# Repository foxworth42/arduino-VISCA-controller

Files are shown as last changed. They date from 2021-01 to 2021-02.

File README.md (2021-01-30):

# Arduino VISCA Controller

## The project is a work-in-progress

This is a project for using an Arduino to send VISCA commands.  This is tailored for interfacing with the
Cisco TelePresence PrecisionHD series of conference cameras (specifically testing with the TTC8-02 12x zoom w/ SDI output).

The TelePresence cameras have a slight quirk to controlling it over VISCA.  To get manual control over the pan/tilt/zoom
rates the camera needs to be sent the IR disable command, otherwise all movements behave with a speed ramp as if you 
were controlling it with an IR remote.

The Arduino Shield board present in the EAGLE directory is intended to make connecting to a TelePresence camera and
wiring I/O easier.  The shield has headers to allow for powering the Arduino off its internal voltage regulator or via
VIN (includes header points to make swapping easy).  There is also a header to provide 12v power over the RJ45
connection to remotely power the camera.  The shield incudes an RS232 transciever so it is ready to plug into the
camera's control port with a standard ethernet cable.

[Cisco TelePresence PrecisionHD User Guide](https://www.cisco.com/c/dam/en/us/td/docs/telepresence/endpoint/camera/precisionhd/user_guide/precisionhd_1080p-720p_camera_user_guide.pdf) (includes supported VISCA command details, cable wiring, etc.)

# Arduino Shield components

|Component|Quantity|Notes|Link|
|---|---|---|---|
|Arduino Shield|1|See EAGLE directory|[Link](https://oshpark.com/shared_projects/oP5dpPBc)|
|RS232 Transciever|1| |[Link](https://www.mouser.com/ProductDetail/968-HIN202IBNZ-T/)|
|0.1uf SMD Capacitor|5| |[Link](https://www.mouser.com/ProductDetail/80-C0805C104J5R/)|
|RJ45 Jack|1| |[Link](https://www.mouser.com/ProductDetail/523-RJHSE-5381/)|
|2pin Molex Header|2|Or whatever header you prefer|[Link](https://www.mouser.com/ProductDetail/538-22-23-2021/)|
|2pin Molex Housing|2| |[Link](https://www.mouser.com/ProductDetail/538-22-01-3027/)|
|3pin Molex Header|4| |[Link](https://www.mouser.com/ProductDetail/538-22-23-2031/)|
|3pin Molex Housing|4| |[Link](https://www.mouser.com/ProductDetail/538-22-01-3037/)|
|4pin Molex Header|2| |[Link](https://www.mouser.com/ProductDetail/538-22-23-2041/)|
|4pin Molex Housing|2| |[Link](https://www.mouser.com/ProductDetail/538-22-01-3047/)|
|8pin Molex Header|2| |[Link](https://www.mouser.com/ProductDetail/538-22-23-2081/)|
|8pin Molex Housing|2| |[Link](https://www.mouser.com/ProductDetail/538-22-01-3087/)|
|Crimp contacts for Molex housings|Lots| |[Link](https://www.mouser.com/ProductDetail/538-08-51-0108-LP/)|
|Crimp tool for Molex contacts|1| |[Link](https://www.amazon.com/gp/product/B078WPT5M1/ref=ppx_yo_dt_b_search_asin_title?ie=UTF8&psc=1)|
|Bunch of single row 2.54 pitch pin headers|Bunch| | |
|10k Ohm Resistors|10| |

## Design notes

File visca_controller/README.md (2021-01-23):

To work on this code in the standard Arduino code editor, rename `src` directory to `visca_controller`, then rename
`visca_controller.cpp` to `visca_controller.ino`

See Jetbrains post about using PlatformIO and CLion for doing Arduno development:

https://blog.jetbrains.com/clion/2020/08/arduino-from-hobby-to-prof-p1/

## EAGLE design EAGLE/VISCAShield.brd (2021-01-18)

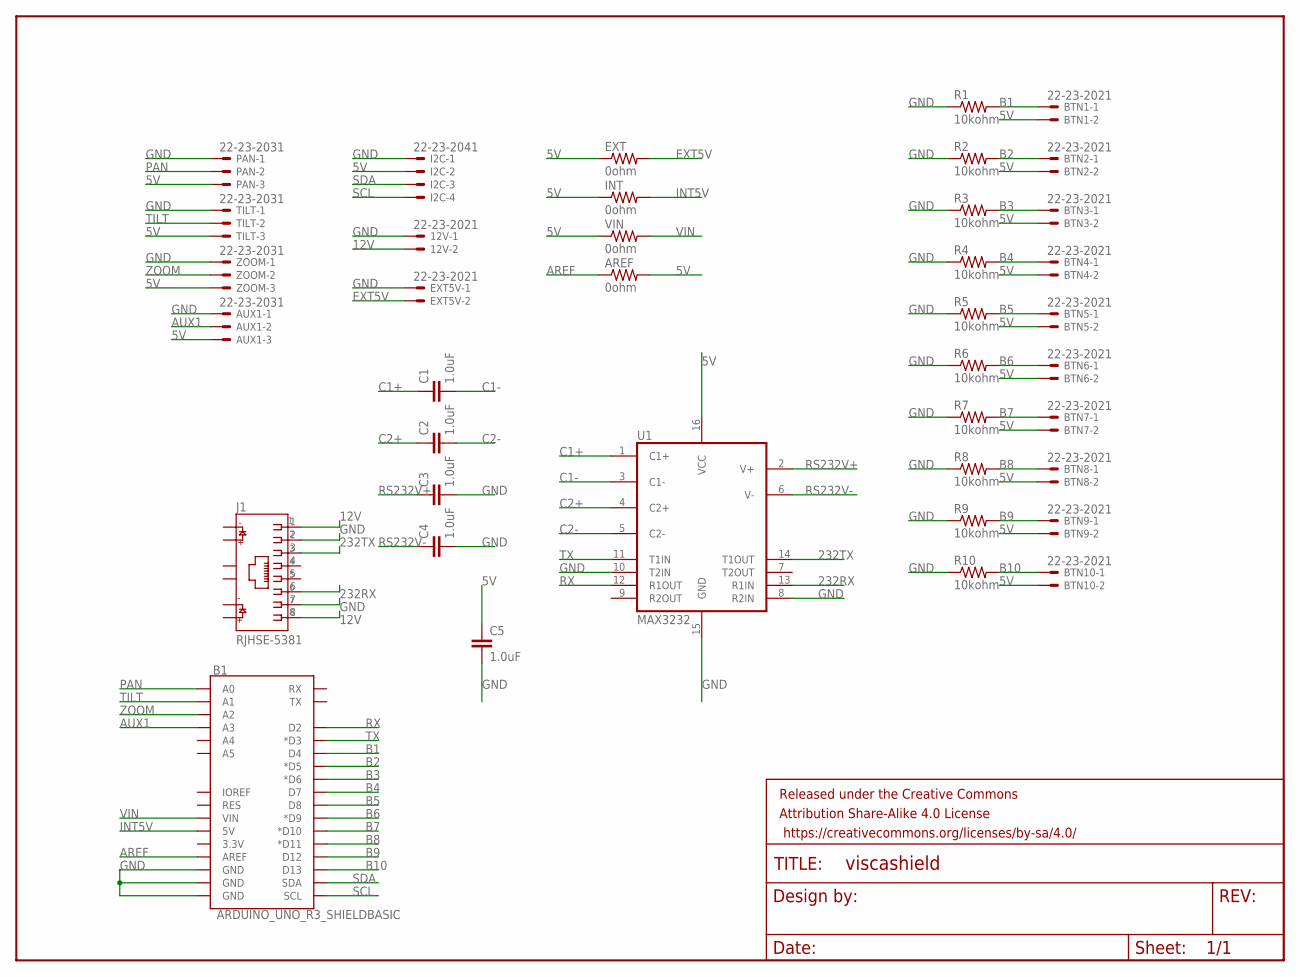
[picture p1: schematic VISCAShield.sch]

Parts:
12V: 22-23-2021
AREF: 0ohm; 0204V
AUX1: 22-23-2031
B1: ARDUINO_UNO_R3_SHIELDBASIC; UNO_R3_SHIELD
BTN1, BTN2, BTN3, BTN4, BTN5, BTN6, BTN7, BTN8, BTN9, BTN10: 22-23-2021
C1, C2, C3, C4, C5: 1.0uF; 0805
EXT: 0ohm; 0204V
EXT5V: 22-23-2021
FRAME1: FRAME-LETTERNO_PACKAGE; DUMMY
I2C: 22-23-2041
INT: 0ohm; 0204V
J1: RJHSE-5381; AMPHENOL_RJHSE-5381
PAN: 22-23-2031
R1, R2, R3, R4, R5, R6, R7, R8, R9, R10: 10kohm; 0204V
TILT: 22-23-2031
U1: MAX3232; SO16
VIN: 0ohm; 0204V
ZOOM: 22-23-2031

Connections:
5V: AREF.2, AUX1.3, BTN1.2, BTN2.2, BTN3.2, BTN4.2, BTN5.2, BTN6.2, BTN7.2, BTN8.2, BTN9.2, BTN10.2, C5.1, EXT.1, I2C.2, INT.1, PAN.3, TILT.3, U1.16 (VCC), VIN.1, ZOOM.3
12V: 12V.2, J1.1, J1.8
232RX: J1.6, U1.13 (R1IN)
232TX: J1.3, U1.14 (T1OUT)
AREF: AREF.1, B1.AREF
AUX1: AUX1.2, B1.A3
B1: B1.D4, BTN1.1, R1.2
B2: B1.D5 (*D5), BTN2.1, R2.2
B3: B1.D6 (*D6), BTN3.1, R3.2
B4: B1.D7, BTN4.1, R4.2
B5: B1.D8, BTN5.1, R5.2
B6: B1.D9 (*D9), BTN6.1, R6.2
B7: B1.D10 (*D10), BTN7.1, R7.2
B8: B1.D11 (*D11), BTN8.1, R8.2
B9: B1.D12, BTN9.1, R9.2
B10: B1.D13, BTN10.1, R10.2
C1+: C1.1, U1.1 (C1+)
C1-: C1.2, U1.3 (C1-)
C2+: C2.1, U1.4 (C2+)
C2-: C2.2, U1.5 (C2-)
EXT5V: EXT.2, EXT5V.2
GND: 12V.1, AUX1.1, B1.GND@0 (GND), B1.GND@1 (GND), B1.GND@2 (GND), C3.2, C4.2, C5.2, EXT5V.1, I2C.1, J1.2, J1.7, PAN.1, R1.1, R2.1, R3.1, R4.1, R5.1, R6.1, R7.1, R8.1, R9.1, R10.1, TILT.1, U1.8 (R2IN), U1.10 (T2IN), U1.15 (GND), ZOOM.1
INT5V: B1.5V, INT.2
PAN: B1.A0, PAN.2
RS232V+: C3.1, U1.2 (V+)
RS232V-: C4.1, U1.6 (V-)
RX: B1.D2, U1.12 (R1OUT)
SCL: B1.SCL, I2C.4
SDA: B1.SDA, I2C.3
TILT: B1.A1, TILT.2
TX: B1.D3 (*D3), U1.11 (T1IN)
VIN: B1.VIN, VIN.2
ZOOM: B1.A2, ZOOM.2

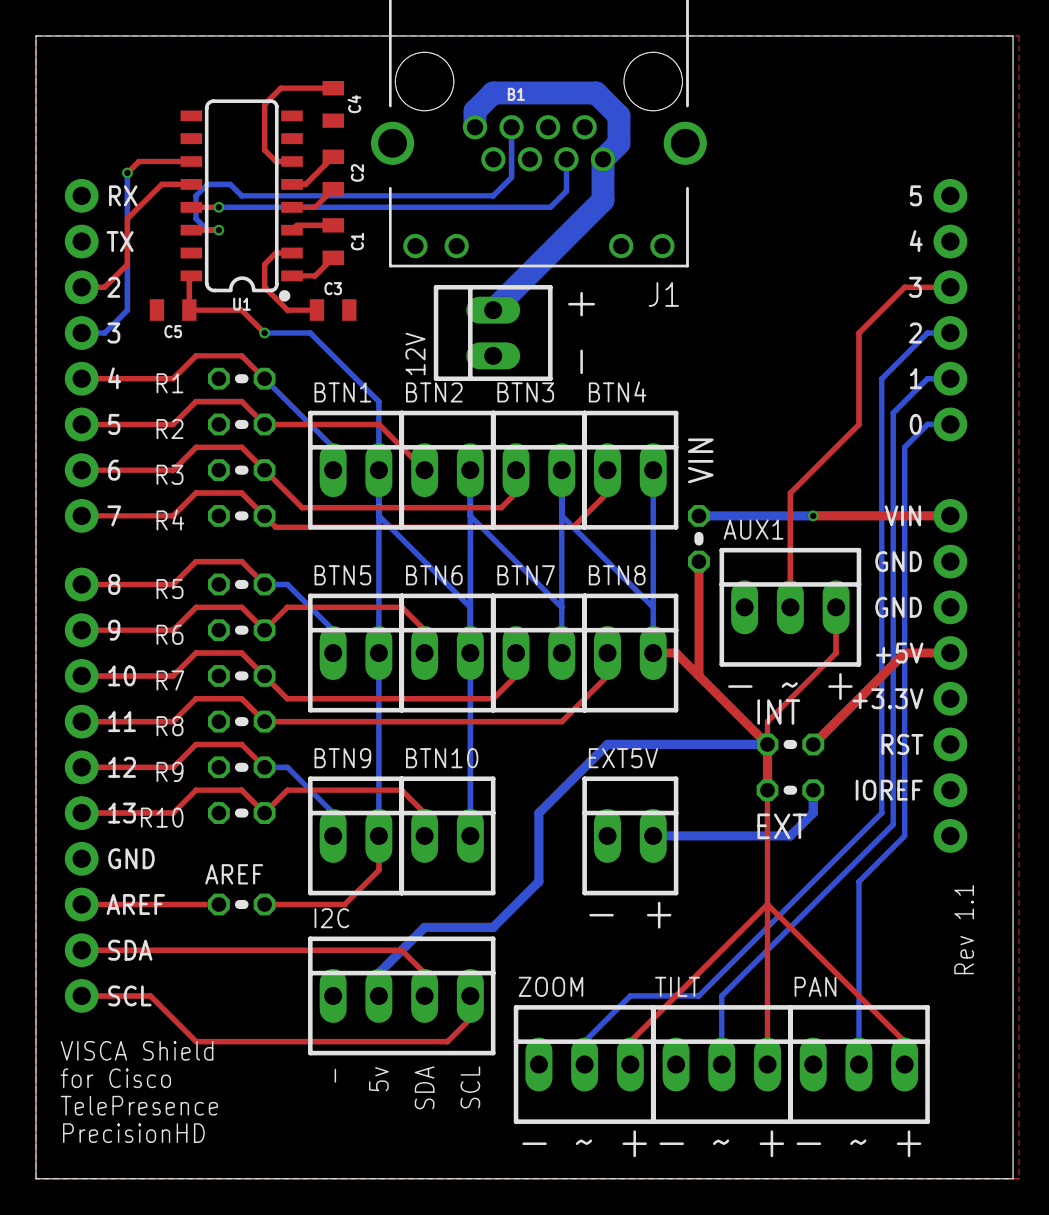
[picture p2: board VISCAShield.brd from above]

Board: 2 copper layers, 54.3 x 63.5 mm, 40 parts (0 on the bottom side), 33 nets.

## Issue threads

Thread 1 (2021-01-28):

Cooperative

shanebou2018, 2021-01-28:
Hello  I'm Shane, I'm located in MA I have 4X PrecisionHD Camera 1080p4X.

I have strong fusion 360 and troubleshooting skills.
I would love to work with you on this project as a tester.
I also could create a 3D printable case to house the controls.

My Email is Shanebou24@gmail.com

Let me know if i can help
Best,
Shane B

P.S,  Obviously this isn't a real Issue/ticket I just didn't know how to reach out.

foxworth42, 2021-02-02:
Hi Shane!  If you you're interested in testing/trying things out I can write up/diagram how I'm currently hooking things up if you want to try and set up your own arduino.

As far as enclosures go, right now I'm looking at using a Hammond 1596EBK (https://www.hammfg.com/part/1595EBK?referer=1197) or the slightly smaller 1596CBK, but it could be worthwhile to look at either doing a fully custom case, or simplifying the creation of the panel insert for a 1596 case (I haven't quite gotten to the point of planning out the enclosure/panel controls quite yet).  I want to use either a 16x2 or a 20x4 I2C display for showing certain parameters eventually, and possibly 2 analog controls (the main joystick, and a second one that can have its function toggled to different things).  I've seen some key panels on ebay that look like they might be good for the various parameter buttons as well, but haven't had a chance to order any to get measurements.

shanebou2018, 2021-02-02:
Thanks for the response. I saw the 16X2 in the code, I'm a big fan.

 I just received a few boards  I should be ready to fully test latter this week.

 This is a photo of the file im working on
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

foxworth42, 2021-02-02:
Nice!

For the buttons I'm hoping 10 will be enough but I was also considering wiring them up as a button matrix to be able to have more buttons (wiring them up that way would change up how the button logic works though).

Right now for buttons I'm looking at buttons for:

+ & - (the function of these would be toggled by other buttons).

Buttons to select the function of +/- & second analog stick (I would love to find a single-axis joystick or center-return knob, but they don't seem that common)
White Balance
Focus
Iris
Gain

Toggles:
Auto Focus toggle
Auto Exposure toggle
Auto White Balance toggle

That would allow for manual control of pretty much all of the exposure parameters, and leave 1 button left over, which is why I was considering the matrix.

shanebou2018, 2021-02-04:
if you did go the matrix route 7 pins could get 12 buttons  and use the rest for rotary encoder or some combination.

I have a few boards put together. I've been testing pan and tilt with success.  I'd like report that for cameras without  dip switches calling up VideoFormat[7]=      { 0x81, 0x01, 0x35, 0x00, 0x01, 0x00, 0xff}; on start is a must.

I haven't been able to make zoom or focus work as of late.

foxworth42, 2021-02-05:
For cameras w/o dip switches, is the issue that they don't output video at all, or defaults to a different resolution/framerate?  It would be pretty easy to have the camera init also spend out format packet just for safety.

shanebou2018, 2021-02-05:
They don't display any video at all unless  told

foxworth42, 2021-02-06:
I've pushed up a change to add the video format to the camera initialization.  Right now it's coded to use 1080p30, but I think down the road it can be made configurable and store the format byte in eeprom.

For zoom/focus, are you trying to do them via analog control, or button control?

shanebou2018, 2021-02-06:
I was testing with analog control and then added to the switch statements. I loaded the new code the setting camera resolution is working

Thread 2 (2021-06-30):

INfor

mshurmer, 2021-06-30:
HI Ed,

I started writing my own for the same camera but I like yours better-   what  analogue joystick are you using?
DO you have any other details on the physical build

My email is   mshurmer@gmail.com

THanks

Matt

foxworth42, 2021-07-07:
I haven't had a bunch of time to work on this lately and haven't done much for the physical build, but I had planned to use this joystick, or similar when I did a final build of it:
https://www.robotshop.com/en/3-axis-joystick-w-button.html

Right now I'm just using a small prototyping box I threw together for hardware testing with 4 separate pots and some buttons on it.

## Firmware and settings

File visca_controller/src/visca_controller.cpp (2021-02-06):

#include "visca_controller.h"

//LiquidCrystal_I2C lcd(0x27,20,4);
SoftwareSerial viscaOutput(VISCARX, VISCATX);

void setup() {
    Serial.begin(115200);
    while (!Serial) { ; // wait for serial port to connect. Needed for native USB port only
    }

    for (uint8_t i = 4; i <= 12; i++) {
        pinMode(i, INPUT);
    }
    viscaOutput.begin(9600);

    initCameras();
    calibrateAnalogControls();

    Serial.println("Started");
}

void loop() {
    handleSerialControl();
    receiveViscaData();
    handleHardwareControl();
}

void handleHardwareControl() {
    processPan(analogRead(PAN));

    processTilt(analogRead(TILT));

    processZoom(analogRead(ZOOM));

    processButtons();
}


void receiveViscaData() {
    static byte ndx = 0;
    while (viscaOutput.available() > 0) {
        byte rc = viscaOutput.read();

        if (rc != 0xFF) {
            viscaMessage[ndx] = rc;
            ndx++;
            if (ndx >= maxViscaMessageSize) {
                ndx = maxViscaMessageSize - 1;
            }
        } else {
            if (viscaMessage[0] == 0x90) {
                if (DEBUG_VISCA == 1) {
                    if (viscaMessage[1] == 0x50) {
                        Serial.println("Command: OK");
                    }
                }

                if (viscaMessage[1] == 0x60) {
                    switch (viscaMessage[2]) {
                        case 0x01:
                            Serial.println("Error: Message length error");
                        case 0x02:
                            Serial.println("Error: Syntax error");
                        case 0x03:
                            Serial.println("Error: Command buffer full");
                        case 0x04:
                            Serial.println("Error: Command cancelled");
                        case 0x05:
                            Serial.println("Error: No socket (to be cancelled)");
                        case 0x41:
                            Serial.println("Error: Command not executable");
                        default:
                            Serial.print("Unknown Error: ");
                            for (uint8_t i = 0; i < ndx; i++) {
                                Serial.print("0x");
                                Serial.print(viscaMessage[i], HEX);
                                Serial.print(" ");
                            }
                            Serial.println("0xFF");
                    }
                }
            }
            ndx = 0;
        }
    }
}


void handleSerialControl() {
    if (Serial.available() > 0) {
        char inChar = Serial.read(); // read incoming serial data:

        switch (inChar) {
            case '1':
                initCameras();
                break;
            case '2':
                toggleFocusControl();
                break;
            case '8':
                sendViscaPacket(callLedOn, sizeof(callLedOn));
                break;
            case '9':
                sendViscaPacket(callLedBlink, sizeof(callLedBlink));
                break;
            case '0':
                sendViscaPacket(callLedOff, sizeof(callLedOff));
                break;
        }
    }
}

unsigned long time_now = 0;
void processButtons() {
    int globalSpeed = analogRead(AUX1);
    int buttonZoomSpeed = map(globalSpeed, 0, 1023, 0, 15);
    if (millis() > time_now + 100) {
        time_now = millis();

        collectCurrentButtonStatus();

        int btn1 = buttons[0];
        if (buttonPressed(btn1) == true) {
            setButtonStatus(btn1, true);
            sendZoomPacket(0x20, buttonZoomSpeed);
        } else if (buttonReleased(btn1) == true) {
            setButtonStatus(btn1, false);
            sendViscaPacket(zoomStop, sizeof(zoomStop));
        }

        int btn2 = buttons[1];
        if (buttonPressed(btn2) == true) {
            setButtonStatus(btn2, true);
            sendZoomPacket(0x30, buttonZoomSpeed);
        } else if (buttonReleased(btn2) == true) {
            setButtonStatus(btn2, false);
            sendViscaPacket(zoomStop, sizeof(zoomStop));
        }

        int btn5 = buttons[4];
        if (buttonPressed(btn5) == true) {
            setButtonStatus(btn5, true);
            initCameras();
        } else if (buttonReleased(btn5) == true) {
            setButtonStatus(btn5, false);
        }
    }
}

void collectCurrentButtonStatus() {
    for (int i = 0; i < (int) (sizeof(buttons) / sizeof(buttons[0])); i++) {
        bitWrite(buttonCurrentStatus, buttons[i], (int) digitalRead(buttons[i]));
    }
}

bool buttonPressed(uint8_t button) {
    return getCurrentButtonStatus(button) == true && getPreviousButtonStatus(button) == false;
}

bool buttonReleased(uint8_t button) {
    return getCurrentButtonStatus(button) == false && getPreviousButtonStatus(button) == true;
}

bool getCurrentButtonStatus(uint8_t button) {
    return (bool) bitRead(buttonCurrentStatus, button);
}

void sendZoomPacket(byte zoomDir, int zoomSpeed) {
    uint8_t zoomDirSpeed = (uint8_t) zoomDir + zoomSpeed;
    zoomCommand[4] = zoomDirSpeed;
    sendViscaPacket(zoomCommand, sizeof(zoomCommand));
}

bool getAnalogCurrentStatus(uint8_t input) {
    return (bool) bitRead(analogCurrentStatus, input);
}

void setAnalogCurrentStatus(uint8_t input, bool status) {
    bitWrite(analogCurrentStatus, input, (int) status);
}

bool getAnalogPreviousStatus(uint8_t input) {
    return (bool) bitRead(analogPreviousStatus, input);
}

void setAnalogPreviousStatus(uint8_t input, bool status) {
    bitWrite(analogPreviousStatus, input, (int) status);
}

bool getPreviousButtonStatus(uint8_t input) {
    return (bool) bitRead(buttonPreviousStatus, input);
}

void setButtonStatus(uint8_t input, bool status) {
    bitWrite(buttonPreviousStatus, input, (int) status);
}

void processZoom(int zoom) {
    if (zoom < zoomThresholds[0] || zoomThresholds[1] < zoom) {
        int zoomMaxSpeed = 15;
        uint8_t zoomSpeed;
        byte zoomDir;
        if (zoom < zoomThresholds[0]) {
            // Zoom Out
            zoomSpeed = map(zoom, zoomThresholds[0], 0, 0, zoomMaxSpeed);
            zoomDir = 0x30;
        } else {
            // Zoom In
            zoomSpeed = map(zoom, zoomThresholds[1], 1018, 0, zoomMaxSpeed);
            zoomDir = 0x20;
        }

        uint8_t zoomDirSpeed = (uint8_t) zoomDir + zoomSpeed;
        if (zoomCommand[4] != zoomDirSpeed) {
            zoomCommand[4] = zoomDirSpeed;
            sendViscaPacket(zoomCommand, sizeof(zoomCommand));
        }
        setAnalogCurrentStatus(2, true);
    } else {
        // Stop Zoom
        if (getAnalogCurrentStatus(2) == true) {
            sendViscaPacket(zoomStop, sizeof(zoomStop));
            setAnalogCurrentStatus(2, false);
        }
    }
}

void processPan(int pan) {
    if (pan < panThresholds[0] || panThresholds[1] < pan) {
        setAnalogCurrentStatus(0, true);
        uint8_t panSpeed;
        if (pan < panThresholds[0]) {
            // Left
            panSpeed = map(pan, panThresholds[0], 0, 0, ptMaxSpeed);
            panTilt[6] = 0x01;
        } else {
            panSpeed = map(pan, panThresholds[1], 1018, 0, ptMaxSpeed);
            // Right
            panTilt[6] = 0x02;
        }

        if (panTilt[4] != panSpeed || getAnalogCurrentStatus(0) != getAnalogPreviousStatus(0)) {
            panTilt[4] = panSpeed;
            sendViscaPacket(panTilt, sizeof(panTilt));
        }
    } else {
        setAnalogCurrentStatus(0, false);
        // Stop Pan
        panTilt[6] = 0x03;
        if (getAnalogCurrentStatus(0) == false && getAnalogPreviousStatus(0) == true) {
            sendViscaPacket(panTilt, sizeof(panTilt));
        }
    }
    setAnalogPreviousStatus(0, getAnalogCurrentStatus(0));
}

void processTilt(int tilt) {
    if (tilt < tiltThresholds[0] || tiltThresholds[1] < tilt) {
        setAnalogCurrentStatus(1, true);
        uint8_t tiltSpeed;
        if (tilt < tiltThresholds[0]) {
            // Down
            tiltSpeed = map(tilt, tiltThresholds[0], 0, 0, ptMaxSpeed);
            panTilt[7] = 0x02;
        } else {
            // Up
            tiltSpeed = map(tilt, tiltThresholds[1], 1018, 0, ptMaxSpeed);
            panTilt[7] = 0x01;
        }

        if (panTilt[5] != tiltSpeed || getAnalogCurrentStatus(1) != getAnalogPreviousStatus(1)) {
            panTilt[5] = tiltSpeed;
            sendViscaPacket(panTilt, sizeof(panTilt));
        }
    } else {
        setAnalogCurrentStatus(1, false);
        // Stop Tilt
        panTilt[7] = 0x03;
        if (getAnalogCurrentStatus(1) == false && getAnalogPreviousStatus(1) == true) {
            sendViscaPacket(panTilt, sizeof(panTilt));
        }
    }
    setAnalogPreviousStatus(1, getAnalogCurrentStatus(1));
}

void toggleFocusControl() {
    sendViscaPacket(focusModeInq, sizeof(focusModeInq));
    delay(100);
    receiveViscaData();
    Serial.print("Current Focus Status: ");
    if (viscaMessage[2] == 2) {
        Serial.println("Auto, Toggling to manual");
        sendViscaPacket(focusManual, sizeof(focusManual));
    } else {
        Serial.println("Manual, Toggling to auto");
        sendViscaPacket(focusAuto, sizeof(focusAuto));
    }
}


void sendViscaPacket(byte *packet, int byteSize) {
    if (DEBUG_VISCA == 1) {
        Serial.print("Sending:");
    }
    for (int i = 0; i < byteSize; i++) {
        if (DEBUG_VISCA == 1) {
            Serial.print(" 0x");
            Serial.print(packet[i], HEX);
        }

        viscaOutput.write(packet[i]);
    }
    if (DEBUG_VISCA == 1) {
        Serial.println();
    }
}

void initCameras() {
    //Send Address command
    Serial.println("Setting addresses...");
    sendViscaPacket(addressCommand, sizeof(addressCommand));
    delay(delayTime);  //delay to allow camera time for next command
    receiveViscaData();

    // Turn off IR control
    Serial.println("Disabling IR control...");
    sendViscaPacket(irOff, sizeof(irOff));
    delay(delayTime);  //delay to allow camera time for next command
    receiveViscaData();

    // Set camera resolution.  Needed for camera w/o DIP switch control of video format.
    Serial.println("Setting camera resolution...");
    sendViscaPacket(videoFormat, sizeof(videoFormat));
    delay(delayTime);  //delay to allow camera time for next command
    receiveViscaData();

    //Send IF_clear command
    Serial.println("Sending IF_Clear...");
    sendViscaPacket(ifClear, sizeof(ifClear));
    delay(delayTime);  //delay to allow camera time for next command
    receiveViscaData();
}

void calibrateAnalogControls() {
    Serial.println("Calibrating analog controls");
    int spread = 70;
    int panZero = analogRead(PAN);
    panThresholds[0] = panZero - spread;
    panThresholds[1] = panZero + spread;

    int tiltZero = analogRead(TILT);
    tiltThresholds[0] = tiltZero - spread;
    tiltThresholds[1] = tiltZero + spread;

    int zoomZero = analogRead(ZOOM);
    zoomThresholds[0] = zoomZero - spread;
    zoomThresholds[1] = zoomZero + spread;

    int auxZero = analogRead(AUX1);
    auxThresholds[0] = auxZero - spread;
    auxThresholds[1] = auxZero + spread;
}

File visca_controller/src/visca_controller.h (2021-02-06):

#ifndef VISCACONTROLLER
#define VISCACONTROLLER

#include <Arduino.h>
//#include <LiquidCrystal_I2C.h>
#include <SoftwareSerial.h>

// Toggle for echoing VISCA commands sent/received over serial monitor.
#define DEBUG_VISCA 0

// Pin assignments from arduno shield.
// Analog inputs
#define PAN 0
#define TILT 1
#define ZOOM 2
#define AUX1 3

// Serial I/O for VISCA communication
#define VISCARX 2
#define VISCATX 3

// Button inputs
#define BTN1 4
#define BTN2 5
#define BTN3 6
#define BTN4 7
#define BTN5 8
#define BTN6 9
#define BTN7 10
#define BTN8 11
#define BTN9 12
#define BTN10 13
const int buttons[] = {
    BTN1,
    BTN2,
    BTN3,
    BTN4,
    BTN5,
    BTN6,
    BTN7,
    BTN8,
    BTN9,
    BTN10
};

const int delayTime = 500;  //Time between commands
const byte maxViscaMessageSize = 16;
byte viscaMessage[maxViscaMessageSize];

byte buttonPreviousStatus = 0x00;
byte buttonCurrentStatus = 0x00;

byte analogCurrentStatus = 0x00;
byte analogPreviousStatus = 0x00;
const int ptMaxSpeed = 5;
int panThresholds[2] = {0, 0};
int tiltThresholds[2] = {0, 0};
int zoomThresholds[2] = {0, 0};
int auxThresholds[2] = {0, 0};

// Pan/Tilt
byte panTilt[9] =       { 0x81, 0x01, 0x06, 0x01, 0x00, 0x00, 0x03, 0x03, 0xFF };
byte panUp[9] =         { 0x81, 0x01, 0x06, 0x01, 0x00, 0x00, 0x03, 0x01, 0xFF }; // 8x 01 06 01 0p 0t 03 01 ff
byte panDown[9] =       { 0x81, 0x01, 0x06, 0x01, 0x00, 0x00, 0x03, 0x02, 0xFF }; // 8x 01 06 01 0p 0t 03 02 ff
byte panLeft[9] =       { 0x81, 0x01, 0x06, 0x01, 0x00, 0x00, 0x01, 0x03, 0xFF }; // 8x 01 06 01 0p 0t 01 03 ff
byte panRight[9] =      { 0x81, 0x01, 0x06, 0x01, 0x00, 0x00, 0x02, 0x03, 0xFF }; // 8x 01 06 01 0p 0t 02 03 ff
byte panUpLeft[9] =     { 0x81, 0x01, 0x06, 0x01, 0x00, 0x00, 0x01, 0x01, 0xFF }; // 8x 01 06 01 0p 0t 01 01 ff
byte panUpRight[9] =    { 0x81, 0x01, 0x06, 0x01, 0x00, 0x00, 0x02, 0x01, 0xFF }; // 8x 01 06 01 0p 0t 02 01 ff
byte panDownLeft[9] =   { 0x81, 0x01, 0x06, 0x01, 0x00, 0x00, 0x01, 0x02, 0xFF }; // 8x 01 06 01 0p 0t 01 02 ff
byte panDownRight[9] =  { 0x81, 0x01, 0x06, 0x01, 0x00, 0x00, 0x02, 0x02, 0xFF }; // 8x 01 06 01 0p 0t 02 02 ff

byte panStop[9] =       { 0x81, 0x01, 0x06, 0x01, 0x09, 0x09, 0x03, 0x03, 0xFF }; // Camera Stop
byte panTiltPosReq[5] = { 0x81, 0x09, 0x06, 0x12, 0xff }; // Resp: y0 50 0p 0q 0r 0s 0t 0u 0v 0w ff ; pqrs: pan position ; tuvw: tilt position

// Zoom
// Tele: 8x 01 04 07 2p ff 
// Wide: 8x 01 04 07 2p ff 
byte zoomCommand[6] = { 0x81, 0x01, 0x04, 0x07, 0x2F, 0xff }; // 8x 01 04 07 2p ff
byte zoomTele[6] =    { 0x81, 0x01, 0x04, 0x07, 0x2F, 0xff }; // 8x 01 04 07 2p ff
byte zoomWide[6] =    { 0x81, 0x01, 0x04, 0x07, 0x3F, 0xff }; // 8x 01 04 07 3p ff
byte zoomStop[6] =    { 0x81, 0x01, 0x04, 0x07, 0x00, 0xff };
byte zoomDirect[9] =  { 0x81, 0x01, 0x04, 0x47, 0x00, 0x00, 0x00, 0x00, 0xff }; // 8x 01 04 47 0p 0q 0r 0s ff pqrs: zoomCommand position
byte zoomPosReq[5] =  { 0x81, 0x09, 0x04, 0x47, 0xff }; // Resp: y0 50 0p 0q 0r 0s ff


// Focus
byte focusAuto[6] =     { 0x81, 0x01, 0x04, 0x38, 0x02, 0xff };
byte focusManual[6] =   { 0x81, 0x01, 0x04, 0x38, 0x03, 0xff };
byte focusDirect[9] =   { 0x81, 0x01, 0x04, 0x48, 0x00, 0x00, 0x00, 0x00, 0xff }; // 8x 01 04 48 0p 0q 0r 0s ff pqrs: focus position
byte focusFar[6] =      { 0x81, 0x01, 0x04, 0x08, 0x20, 0xff };
byte focusNear[6] =     { 0x81, 0x01, 0x04, 0x08, 0x30, 0xff };
byte focusStop[6] =     { 0x81, 0x01, 0x04, 0x08, 0x00, 0xff };
byte focusModeInq[5] =  { 0x81, 0x09, 0x04, 0x38, 0xff }; // Resp: y0 50 0p ff ; p=2: Auto, p=3: Manual

// Iris / Gain
byte aeAuto[6] =      { 0x81, 0x01, 0x04, 0x39, 0x00, 0xff };
byte aeManual[6] =    { 0x81, 0x01, 0x04, 0x39, 0x03, 0xff };
byte irisDirect[9] =  { 0x81, 0x01, 0x04, 0x4B, 0x00, 0x00, 0x00, 0x00, 0xff }; // 8x 01 04 4B 0p 0q 0r 0s ff pqrs: Iris position, range 0..50
byte gainDirect[9] =  { 0x81, 0x01, 0x04, 0x4C, 0x00, 0x00, 0x00, 0x00, 0xff }; // 8x 01 04 4c 0p 0q 0r 0s ff pqrs: Gain position, values: 12-21dB.
byte aeModeInq[5] =   { 0x81, 0x09, 0x04, 0x39, 0xff }; // Resp: y0 50 0p ff ; p=0: Auto, p=3: Manual

// White Balance
byte wbAuto[6] =        { 0x81, 0x01, 0x04, 0x35, 0x00, 0xff };
byte wbTableManual[6] = { 0x81, 0x01, 0x04, 0x35, 0x06, 0xff };
byte wbTableDirect[9] = { 0x81, 0x01, 0x04, 0x75, 0x00, 0x00, 0x0, 0x00, 0xff }; // 8x 01 04 75 0p 0q 0r 0s ff pqrs = wb table.

// Config
byte addressCommand[4] = {0x88, 0x30, 0x01, 0xFF }; // Sets camera address (Needed for Daisy Chaining)
byte ifClear[5] =        {0x88, 0x01, 0x00, 0x01, 0xFF }; // Checks to see if communication line is clear
byte irOff[6] =          {0x81, 0x01, 0x06, 0x09, 0x03, 0xff }; // Turn off IR control (required for speed control of Pan/Tilt on TelePresence cameras)
byte callLedOn[6] =     { 0x81, 0x01, 0x33, 0x01, 0x01, 0xff };
byte callLedOff[6] =    { 0x81, 0x01, 0x33, 0x01, 0x00, 0xff };
byte callLedBlink[6] =  { 0x81, 0x01, 0x33, 0x01, 0x02, 0xff };
/*
 * Video formats values:
 * Value    HDMI    SDI
 * 0x00     1080p25 1080p25
 * 0x01     1080p30 1080p30
 * 0x02     1080p50 720p50
 * 0x03     1080p60 720p60
 * 0x04     720p25  720p25
 * 0x05     720p30  720p30
 * 0x06     720p50  720p50
 * 0x07     720p60  720p60
 */
byte format = 0x01;
byte videoFormat[7] = { 0x81, 0x01, 0x35, 0x00, format, 0x00, 0xff }; // 8x 01 35 0p 0q 0r ff p = reserved, q = video mode, r = Used in PrecisionHD 720p camera.

void sendViscaPacket(byte *packet, int byteSize);
void handleHardwareControl();
void receiveViscaData();
void handleSerialControl();
void processButtons();
void collectCurrentButtonStatus();
bool buttonPressed(uint8_t button);
bool buttonReleased(uint8_t button);
bool getCurrentButtonStatus(uint8_t button);
void sendZoomPacket(byte zoomDir, int zoomSpeed);
bool getAnalogCurrentStatus(uint8_t input);
void setAnalogCurrentStatus(uint8_t input, bool status);
bool getAnalogPreviousStatus(uint8_t input);
void setAnalogPreviousStatus(uint8_t input, bool status);
bool getPreviousButtonStatus(uint8_t input);
void setButtonStatus(uint8_t input, bool status);
void processPan(int pan);
void processTilt(int tilt);
void processZoom(int zoom);
void toggleFocusControl();
void initCameras();
void calibrateAnalogControls();

#endif

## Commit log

2020-01-04 Initial commit of arduino shield design.
    VISCA shield that exposes all pins to headers ready to be wired to 10 buttons,
    6 pots, I2C, with the option for external 5v, as well as an RJ45 jack wired
    for connecting to Cisco PrecisionHD PTZ cameras.
    [VISCAShield.brd, VISCAShield.sch]
2020-01-04 initial commit of arduino sketch for VISCA controller.
2020-01-12 Some revisions.
    [VISCAShield.brd, VISCAShield.sch]
2020-01-12 Remove I2C display for now until I start to make use of it.
2020-01-13 Add optional AREF input jumper. Clean up unused nets from schematic.
    [VISCAShield.brd, VISCAShield.sch]
2021-01-17 Successful build of Visca shield & more testing of control code.
    [VISCAShield.brd, VISCAShield.sch]
2021-01-18 Increase trace width on 12v power to RJ45 jack.
    [VISCAShield.brd]
2021-01-18 Add BOM for shield.
2021-01-20 Add note about opening Arduino code in the Arduino editor.
2021-01-23 Add automatic analog control zero point/movement calibration & more cleanup/refinement.
2021-01-23 Fix issue with not being able to pan/tilt at the slowest possible speed.
    [visca_controller.cpp, visca_controller.h]
2021-02-06 Add video format to camera initialization.

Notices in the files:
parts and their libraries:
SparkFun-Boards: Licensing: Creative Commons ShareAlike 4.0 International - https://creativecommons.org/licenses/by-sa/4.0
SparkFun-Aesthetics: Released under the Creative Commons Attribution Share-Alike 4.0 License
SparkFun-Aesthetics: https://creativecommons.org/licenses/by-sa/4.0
